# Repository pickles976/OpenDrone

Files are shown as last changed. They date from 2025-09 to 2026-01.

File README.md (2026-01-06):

# OpenDrone

OpenDrone is my attempt at creating a cheap, modular, easy-to-build and easy-to-fly series fixed-wing FPV drones. 

As a total beginner, I am learning as I go and prioritizing simplicity at every step. I try to avoid complex/skilled construction tricks.

I am making drones in different "weight" categories, starting with the [Mockingbird](./Mockingbird/README.md).

The goal is to have a collection of simple and cheap open-source drone designs with flight characteristics that make them useful tools, and not just toys. Long flight times, large payloads, modularity, and field-repairability are all design goals. The goal is to allow small groups of people to mass produce SAR drones without needing a whole lot of initial investment. A single maker or tinkerer should be able to assemble a small fleet of drones in their garage with a 3D printer, some hand tools, and [Made in China](https://evcraft.en.made-in-china.com) account.

## Educational Resources  

You can assemble one of these drones just by blindly following the build guide, but I also want to educate the end-user to enable them to modify and make their own drones. When I started this project, I had no knowledge of CAD, airplane design, or RC systems. I am still a novice, but I have the fundamentals down to build my own planes.

This list is by no means comprehensive, it is just the resources that *I* used. Feel free to open a pull request if you have suggestions. No higher education is needed to understand anything in this guide, just basic algebra and high school physics.

### Legal Stuff

Boring legal shit. Don't do anything illegal, please be respectful of others and their property. Don't get yourself in trouble.

#### AMA

The [Academy of Model Aeronautics](https://www.modelaircraft.org/) is a great resource. For about $90 a year you get $2.5M of liability insurance. Many clubs won't let you fly without a membership. They have a tool [here](https://www.modelaircraft.org/club-finder) for finding clubs and airfields near you.

#### FAA

The [FAA Rules](https://www.faa.gov/uas/recreational_flyers) has a lot of rules about flying drones. If you fly at a club, they will let you know all of the rules.

### Learning to Fly

Your local hobbyist club will hopefully be eager to teach you. I learned to fly on an HobbyZone Aeroscout in a few sessions. RealFlight is a simulator that costs about $90 and I have heard very good things about it, but have never tried it. For quad FPV, I recommend Liftoff simulator and a cheap [fpv sim controller](https://www.amazon.com/LiteRadio-Simulator-Controller-Platforms-Uncrashed-VelociDrone/dp/B0FMFCTSXV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) or something like the [Radiomaster Pocket](https://www.amazon.com/Radiomaster-Pocket-Transmitter-Lightweight-ELRS-Charcoal/dp/B0DXPLH726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) if you are willing to spend more money for a real controller.

### CAD Basics  

I use FreeCAD because this project should be accessible to as many people as possible. While other CAD programs are older, have more features, and are easier to use, but FOSS is under the control of the people. Not corporations or governments. For this reason, this guide is 100% FOSS.

[MangoJelly FreeCAD Tutorials](https://www.youtube.com/playlist?list=PLWuyJLVUNtc3UYXXfSglVpfWdX31F-e5S)  

The MangoJelly tutorials are incredible. He covers all of the fundamental skills needed to make parts in FreeCAD.  
(Total time to follow along with playlist, 24-48 hrs)  

[More FreeCAD Tutorials](https://youtube.com/playlist?list=PL10-2AjHWnW4To6a0luIpGCgNKQrAo04l&si=9Q5ZE8DqiylH0JF-)  

Here are more tutorials, with a guide on making a Lego minifigure based off of observation and measurements. These tutorials are excellent for thinking about how to replicate parts. Some of the first parts I designed were custom Lego accessories. (Total time to follow along with playlist, 10-20 hrs)

### Plastic Manufacturing Basics  

#### Plastic Part Design

It is easier to design good plastic parts if you understand the fundamentals of plastics and plastic design. The book [Designing Plastic Parts for Assembly](https://www.amazon.com/Designing-Plastic-Parts-Assembly-8E/dp/1569906688) is specifically about injection molding, but concepts like wall thickness, ribs, and filleting are applicable to 3D printed part design. I would recommend using the site [Anna's Archive](https://annas-archive.org/) to find a free copy of this book. It is very dense with a lot of information, so just read the first few chapters casually to understand the basics.

[Functional Design for 3D Printing](https://www.amazon.com/Functional-Design-Printing-2nd-Designing/dp/1511572027) is also a good resource.

#### 3D Printing

Personally I have a Bambu Labs A1 mini printer. It works extremely well out of the box with PLA and PETG filaments. For more pesky filaments like LW-PLA or TPU, you will need to play around with the settings to get things to work.

[Orca Slicer](https://orca-slicer.com/) is a fork of Bambu Studio with some added features. It is what I use for slicing my prints.

A video on [3D printing basics](https://www.youtube.com/watch?v=2vFdwz4U1VQ).  
[3D printing quality guide](https://www.youtube.com/watch?v=YPAXeBuq9qU)  

Here are some excellent videos on making snap-fit parts and making parts stronger:  
[Connecting Parts](https://www.youtube.com/watch?v=djm5tCFn9S0)  
[Part Strength](https://www.youtube.com/watch?v=Lq-SoGgKOcQ)  

### Aeronautical Engineering Basics

#### Forces of Flight

[A video on the Four Forces of Flight](https://www.youtube.com/watch?v=zKSNudPl9UI)  

#### Lift

[Principles of Flight (Lift)](https://www.youtube.com/watch?v=38X7UfPSdss)  
[Lift and Angle of Attack](https://www.youtube.com/watch?v=40uhfWbZH6g)  

#### Drag

Drag is a single force with multiple components. Parasitic Drag (consisting of skin friction drag and form drag), and Lift-Induced Drag (caused by turbulent airflow in the wake of the plane).

[Components of Drag](https://en.wikipedia.org/wiki/Drag_(physics))  
[Principles of Flight (Induced Drag)](https://www.youtube.com/watch?v=ohEiPg1q0TE)  
[Principles of Flight (Parasite Drag)](https://www.youtube.com/watch?v=V8vwyzt54_c)  

#### Tools

[Static Thrust Calculator](https://rcplanes.online/calc_thrust.htm)    
[ecalc](https://www.ecalc.ch/) prop sizing, performance estimation, much more.    

#### Airfoil Design

Airfoil design can get pretty complicated. I read a lot and ended up going with a simple Armin Wing, due to the fact that it would be nearly impossible for me to experimentally test a wing design without a wind tunnel or accurate cross-sectional measurements. However, wing design concepts are still good for understanding the basics of things like MAC and wing loading.
[Wing Design basics](https://www.youtube.com/watch?v=QHNtD8ChRZU)

I recommend watching these videos and building the glider from the video. Building the glider gave me a great sense of intuition for designing stable aircraft.
[RC Plane Design Basics](https://www.youtube.com/watch?v=CXvHv2EXcF8)
[Foamboard Glider Design](https://www.youtube.com/watch?v=YzqS_NjTxps)

#### Balance and Stability

[Aircraft Stability Concepts](https://www.youtube.com/watch?v=BWx8m4G0nEc)  
[Aircraft Stability Practical](https://www.youtube.com/watch?v=2t6tT77QFW4)  
[Flitetest, positioning the Center of Gravity](https://www.flitetest.com/articles/where-should-an-rc-airplane-center-of-gravity-be)  

### RC Basics

[Express LRS](https://www.youtube.com/watch?v=N0ajKoef3qs)  
[RC Battery Basics](https://www.youtube.com/watch?v=D98e2lRe2O8)   
[Safe Battery Charging](https://www.youtube.com/watch?v=MeAlEUb_vgg)
[Brushless DC Motors Explained](https://www.youtube.com/watch?v=yiD5nCfmbV0)  
[Servos](https://www.youtube.com/watch?v=tHOH-bYjR4k)  
[Joshua Bardwell Soldering](https://www.youtube.com/watch?v=GoPT69y98pY)  
[MuteFPV Soldering](https://www.youtube.com/watch?v=czXJevPWIsA)  
[SpeedyBee F405 wing setup](https://www.youtube.com/watch?v=LW57cibsMxY)  

[Flite Test Tutorial Series](https://youtube.com/playlist?list=PL6IuSFWz4ktvupu_gxw1vn-sjBGOkJFHV&si=_ucsjRaIemd7ZCSS) 

If you want to get deeper into electronics concepts, I recommend [Practical Electronics for Inventors, Fourth Edition](https://www.amazon.com/Practical-Electronics-Inventors-Fourth-Scherz/dp/1259587541)

### Autonomy

TODO

### FPV

TODO

# TODO: 

- [ ] stuff $100
    - [x] XT60 cable kit
    - [x] SG09 servos
    - [x] Fast-printing PETG
    - [x] FPV solder practice board
    - [x] Arms for holding boards while soldering
    - [x] brass sponge
    - [x] silicone mat
    - [x] flat plate for printing
    - [x] shorter servo connectors
- [ ] fpv
    - [ ] Eachine ev800D goggles
    - [ ] EWRF TS5823 5.8GHz 40CH 600mW FPV TX and camera

https://www.amazon.com/TMH-Adapter-Connector-Silicone-Battery/dp/B0DNT2R5JN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

# Further Reading
Aircraft Design a Conceptual Approach
Basics of Model Aircraft Design

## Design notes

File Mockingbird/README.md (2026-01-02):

# MockingBird

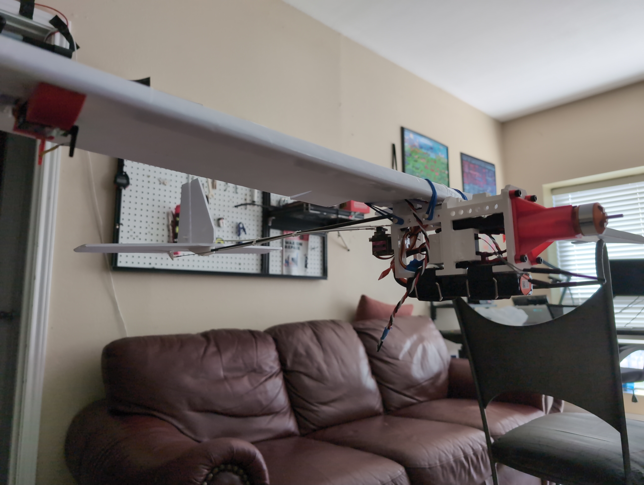
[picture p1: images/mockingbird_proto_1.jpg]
Mockingbird Prototype from Below

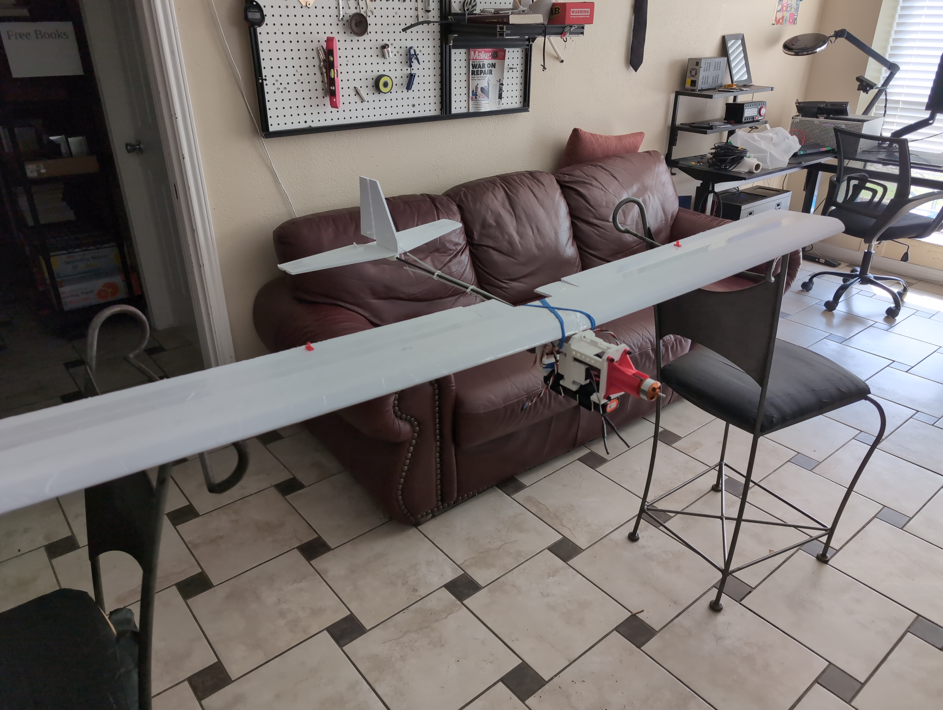
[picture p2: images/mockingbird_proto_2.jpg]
Mockingbird Prototype from above
  

Mockingbird is intended to be the cheapest and simplest drone to make. It has an initial setup cost of about $250 (not including tools), but the unit cost is about $90. Most of that is the electronics.

Every component is designed to fit on the printing plate of a Bambu A1 mini. The design is intended to be slow-flying and stable, with glider-like performance characteristics. The wings can be constructed out of a single piece of 20"x30" 5mm thick foamboard. The design supports multiple receivers and batteries, with variable wing positioning to adjust the center of gravity accordingly.

# Wing Specs

- Armin Wing Design
- 2 parts, 10" x 30" foamboard
- assembled dimensions
    - chord: 0.15m
    - wingspan: 1.524m
    - area: 0.2286m^2
- aspect ratio: 10.15 (wingspan squared over wing area)
- taper ratio: 1

An aspect ratio of 10 just barely puts us into glider territory. The wing design is a modified [Armin wing design](https://www.youtube.com/watch?v=karr67ZYho4) tweaked to take up exactly one sheet of 20"x30" foamboard.

### Equations
```math
Aspect Ratio = \frac SA
```

```math
\begin{aligned}
Wing Loading = \frac WA \\
Wing Loading = \frac 12 \rho V_{stall}^2 C_{Lift Max}  \\
V_{stall} = \sqrt{\frac {2\frac WA} {\rho C_{Lift Max}}} \\

\rho = 1.225 \\
C_{Lift Max} = 1.5

\end{aligned}
```

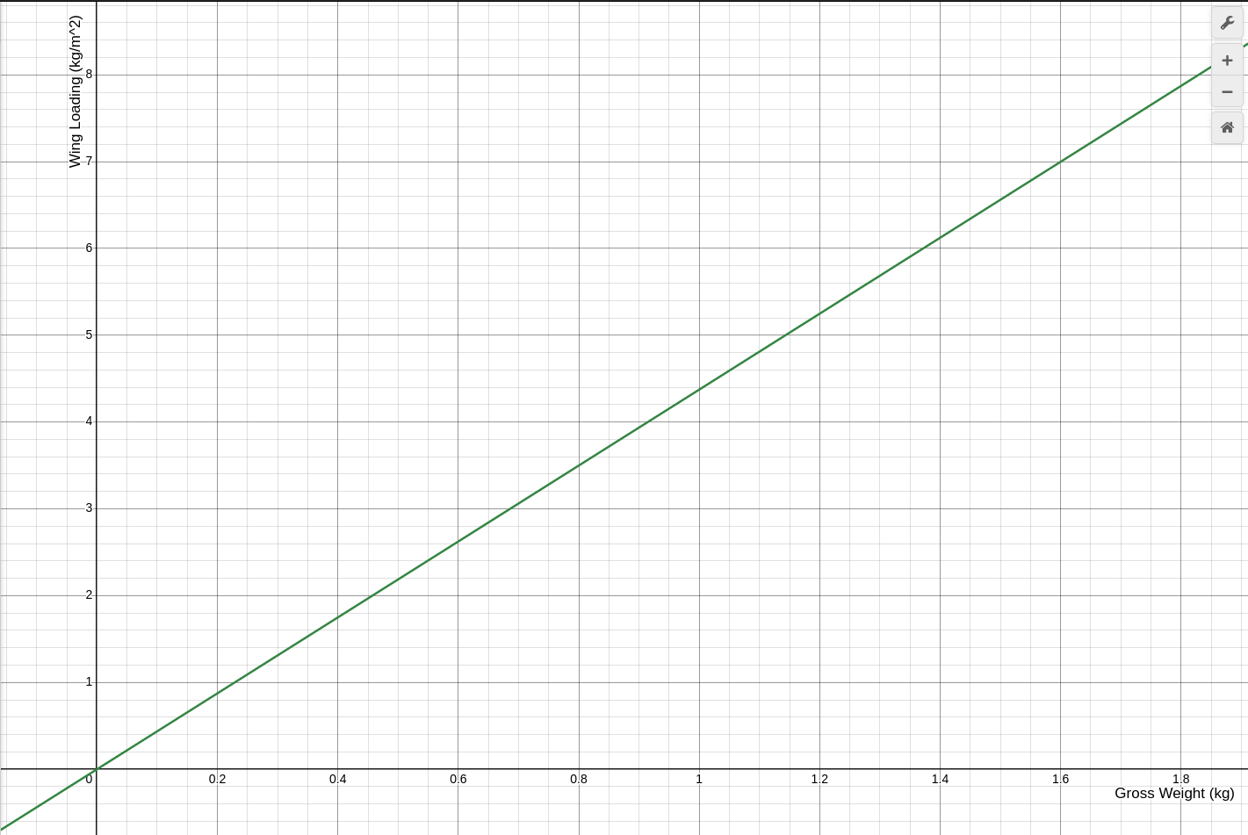
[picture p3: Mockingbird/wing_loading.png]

Wing Loading Curve  

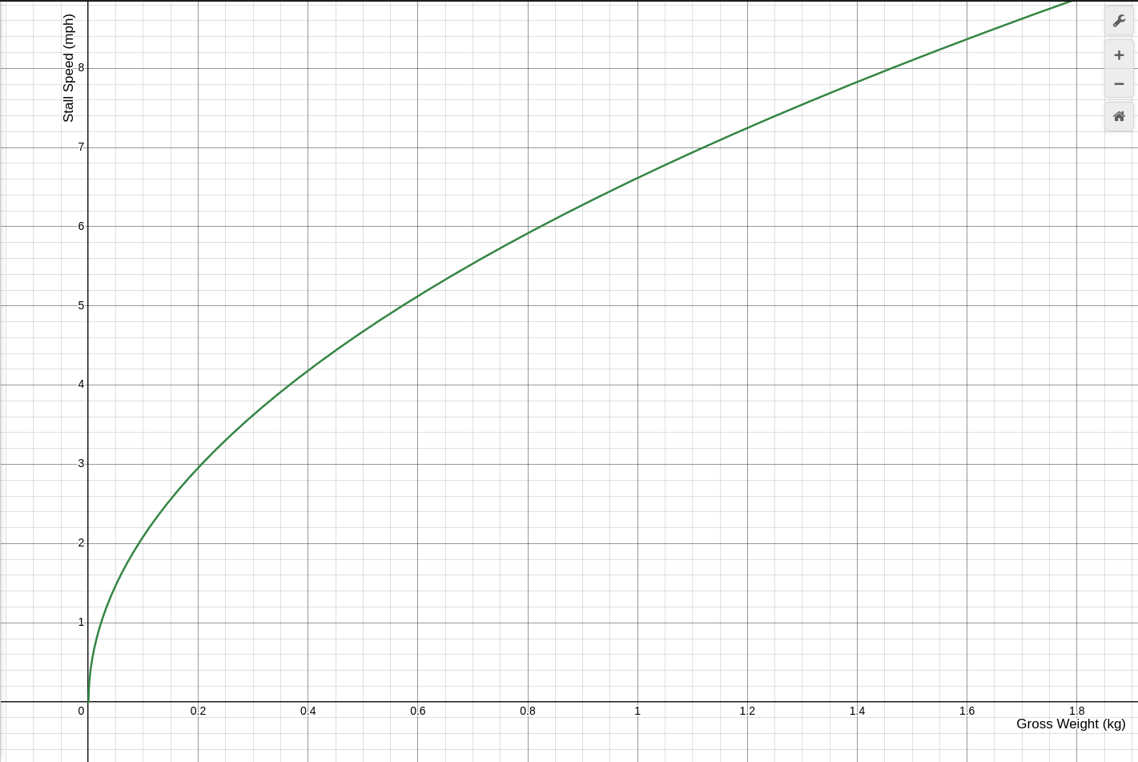
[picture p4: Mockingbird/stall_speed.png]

Stall Speed Curve   

Target weight is 650g, which would give us a stall speed of ~5mph.

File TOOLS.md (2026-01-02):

# Tools

An exhaustive list of tools required to build any of the designs in this guide.

## Assembly
Bambu A1 Mini or Larger $250
X-Acto knife $1 Harbor Freight
cutting surface $10
Printer
Metal Ruler $1
Large Hot Glue gun $20
Large Hot Glue sticks $10

## Control

RadioMaster Pocket $80
18650 Battery for radio (2x) $16
Battery Charger $30-$50

## Electronics

Pinecil soldering iron $40
100W USB-C charger for Pinecil $30

## Design

Digital Calipers (Vinca brand) $22

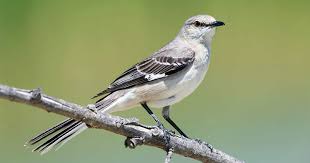
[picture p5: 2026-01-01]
images/mockingbird.jpeg

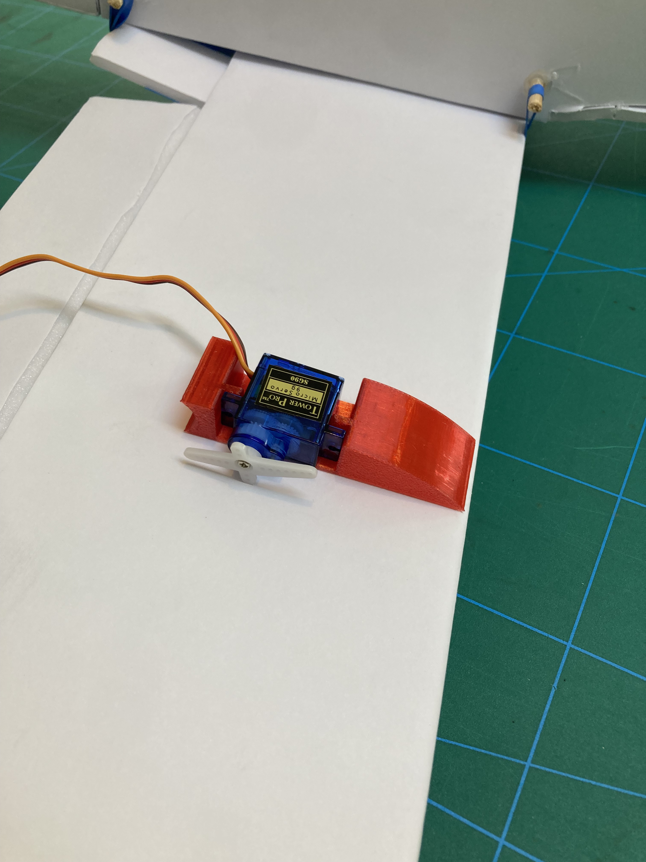
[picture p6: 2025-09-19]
images/servo_fairing.jpg

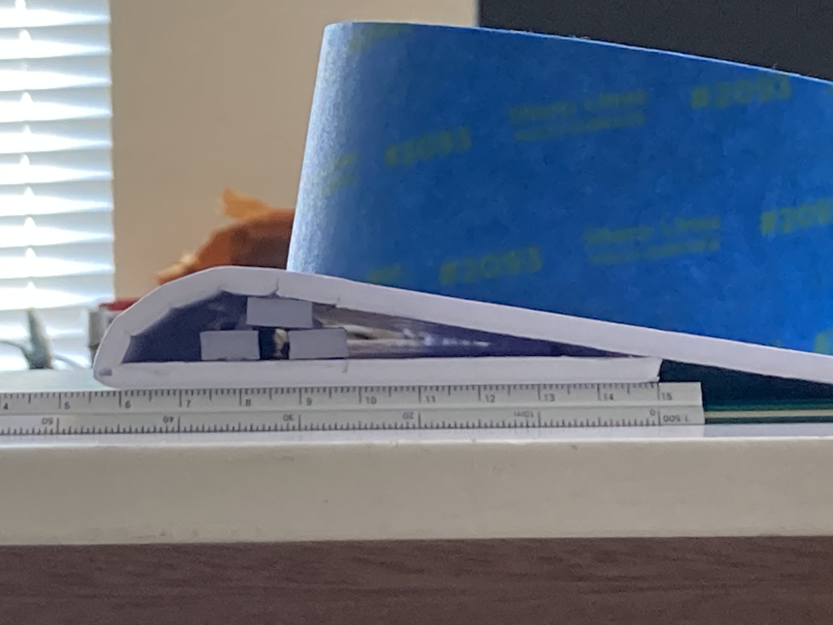
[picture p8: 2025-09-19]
Utilities/Reference Images/wing_cross_section.jpg

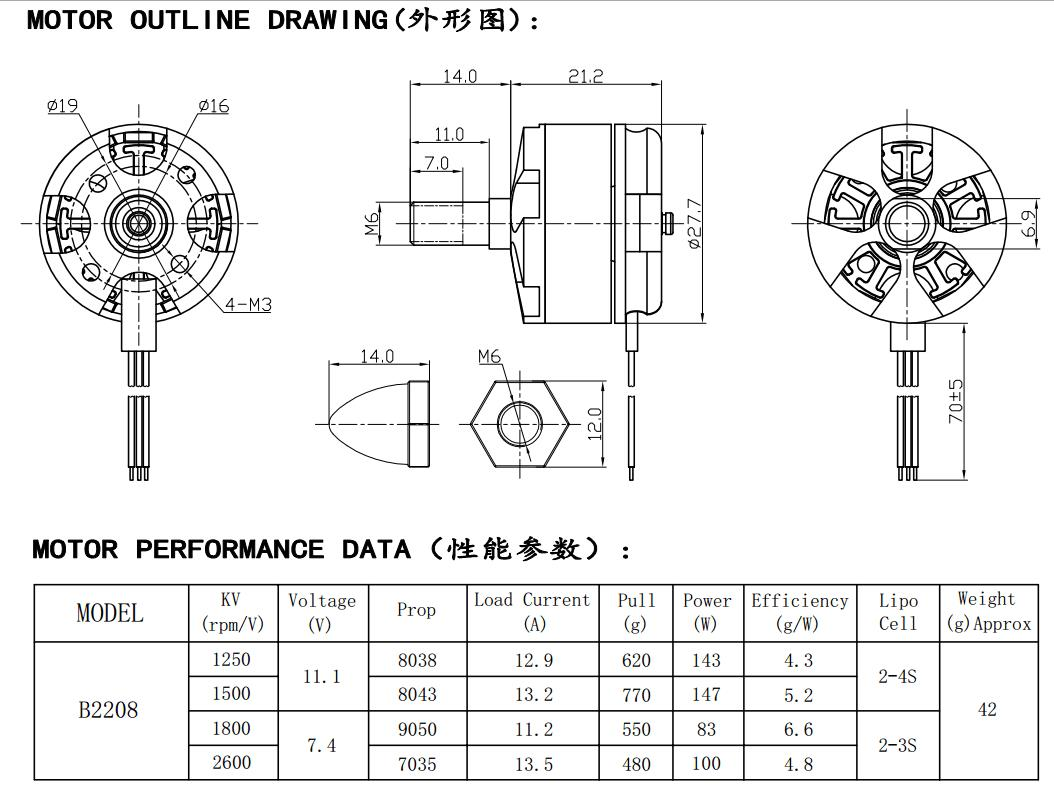
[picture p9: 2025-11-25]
Utilities/Reference Images/BR_2208.png

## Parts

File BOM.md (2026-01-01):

## Bill of Materials

20"x30" foamboard (2)
Carbon Fiber rod (5mm diameter) (2)
Wooden stake (5mm diameter) (2)
Servo fairings (2)
2S or 3S battery
Motor
Prop
Servo extenders
9g Servo (4)
front cap
end cap
tailfin
flight computer
ESC 

sticky side velcro
velcro straps
Lighweight PLA

## Cost

| Item | cost | qty for planes | cost per unit |
|---|---|---|---|
| Hook and Loop Velcro | 13 | 16 | 0.8125 |
| Adhesive Velcro | 10 | 360 | 0.02777777778 |
| M2 screws | 10 | 25 | 0.4 |
| Push rods | 13 | 10 | 1.3 |
| ELRS receiver | 19 | 1 | 19 |
| 30A ESC | 13 | 1 | 13 |
| 9g servo | 14 | 1 | 14 |
| 5x300mm carbon fiber rods | 10 | 5 | 2 |
| 3D printer filament | 50 | 20 | 2.5 |
| 0.8mm wire | 9 | 100 | 0.09 |
| 20"x30" 5mm foamboard | 54 | 18 | 3 |
| 5200mAh 2s | 22 | 2 | 11 |
| 800-1400kv motor | 12 | 1 | 12 |
| Dowels | 7 | 30 |  0.2333333333 |
| rubber bands |  5.3 | 32 | 0.165625 |
| servo extender | 10 | 2.5 | 4 |
| 8x4 properller | 12 | 3 | 4 |

Startup Cost: $283
Unit Cost $88

## Mass Budget

#### Electronics

| Item | Weight per unit | Qty | Total |
|---|---|-----|---|
| Battery | 172g | 1 | 172g  |
| ESC | 32g | 1 | 32g |
| Receiver | 15g | 1 | 15g |
| Motor | 41g | 1 | 41g |
| Servos | 12g | 4 | 48g |
| Servo Extender | 10g | 2 | 20g |
| Straps | ??? | ? | ??? |
| | | | 328g  |

#### Aerofoils

| Item | Weight per unit | Qty | Total |
|---|---|-----|---|
| Wings | 220g | 1 | 220g  |
| Carbon Fiber Rod | 11g | 2 | 22g |
| Wooden Stake | 2g | 2 | 4g |
| Servo Fairings | 3g | 2 | 6g |
| Tailfin Assembly | 27g | 1 | 27g |
| | | | 279g  |

#### Pod

| Item | Weight per unit | Qty | Total |
|---|---|-----|---|
| Motor Mount | 18g | 1 | 18g |
| Electronics Payload | 56g | 1 | 56g |
| M4 Screws | 3g | 8 | 24g |
| Servo Holder | ??? | 1 | ??? |
| Front Cap | ??? | 1 | ??? |
| End Cap | ??? | 1 | ??? |
| Body Fairing | ??? | 1 | ??? |
| | | | 88g |

TOTAL: 708g
ACTUAL MEASURED: 720g

#### Autonomy
flight computer -- 42g
GNSS -- 15g

# Tools 
x-acto knife
cutting surface
packing tape
fine sharpie
masking tape
squishy adhesive
twist ties
hex wrench set
small phillips head
hot glue gun
3D printer (Bambu A1 recommended)
PETG filament
LW-PLA filament
rubber bands
needle-nose pliers
scissors

## Optional
shrink-wrap
mallet

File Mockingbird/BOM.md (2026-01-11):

## Bill of Materials

2S 2200mAh battery   (1)  
SG09  Servo (4)  
30A Electronic Speed Controller (1)  
Motor (800-1400kv) (1)  
Servo extension cables (12") (2)  
Propeller (8x4E) (1)  
BetaFPV ELRS Mini Receiver (1)  

20"x30" foamboard (2)    
Carbon Fiber rod (5mm diameter) (2)    
Wooden Dowel (5mm diameter) (2)    
Adhesive velcro strips (2")  
Velcro straps (12") (2)  
PETG filament (100g)  
PLA or LW-PLA filament (100g)  
Hot Glue (100g)  

**Optional (for autonomy)**
SpeedyBee F405 Wing flight computer (1)  
Beitian BF-180GNSS module (1)

# Tools 
x-acto knife or snap-blade utility knife 
cutting surface (cutting mat on flat table)  
packing tape  
fine sharpie  
masking tape  
squishy adhesive  
twist ties  
hex wrench set  
small phillips head screwdriver (for servo screws)  
hot glue gun  
3D printer (Bambu A1 recommended)  
rubber bands  
needle-nose pliers  
scissors  

**Optional**  
shrink-wrap  
mallet  

## Cost

| Item | cost | qty for planes | cost per unit |
|---|---|---|---|
| Hook and Loop Velcro | 13 | 16 | 0.8125 |
| Adhesive Velcro | 10 | 360 | 0.02777777778 |
| M2 screws | 10 | 25 | 0.4 |
| Push rods | 13 | 10 | 1.3 |
| ELRS receiver | 19 | 1 | 19 |
| 30A ESC | 13 | 1 | 13 |
| 9g servo | 14 | 1 | 14 |
| 5x300mm carbon fiber rods | 10 | 5 | 2 |
| 3D printer filament | 50 | 20 | 2.5 |
| 0.8mm wire | 9 | 100 | 0.09 |
| 20"x30" 5mm foamboard | 54 | 18 | 3 |
| 5200mAh 2s | 22 | 2 | 11 |
| 800-1400kv motor | 12 | 1 | 12 |
| Dowels | 7 | 30 |  0.2333333333 |
| rubber bands |  5.3 | 32 | 0.165625 |
| servo extender | 10 | 2.5 | 4 |
| 8x4 properller | 12 | 3 | 4 |

Startup Cost: $283
Unit Cost $88

# Mass Budget

## Electronics

| Item | Weight per unit | Qty | Total |
|---|---|-----|---|
| Battery | 172g | 1 | 172g  |
| ESC | 32g | 1 | 32g |
| Receiver | 15g | 1 | 15g |
| Motor | 41g | 1 | 41g |
| SG 90 Servos | 19g | 4 | 36g |
| 12" Servo Extenders | 10g | 2 | 20g |
| Straps | ??? | ? | ??? |
| | | | 328g  |

## Aerofoils

| Item | Weight per unit | Qty | Total |
|---|---|-----|---|
| Wings | 220g | 1 | 220g  |
| Carbon Fiber Rod | 11g | 2 | 22g |
| Wooden Stake | 2g | 2 | 4g |
| Servo Fairings | 3g | 2 | 6g |
| Tailfin Assembly | 27g | 1 | 27g |
| | | | 279g  |

## Pod

| Item | Weight per unit | Qty | Total |
|---|---|-----|---|
| Motor Mount | 18g | 1 | 18g |
| Electronics Payload | 56g | 1 | 56g |
| M4 Screws | 3g | 8 | 24g |
| Servo Holder | ??? | 1 | ??? |
| Front Cap | ??? | 1 | ??? |
| End Cap | ??? | 1 | ??? |
| Body Fairing | ??? | 1 | ??? |
| | | | 88g |
  
TOTAL: 708g  
ACTUAL MEASURED: 720g  

## Autonomy
flight computer -- 42g
GNSS -- 15g

TOTAL + Autonomy: 780g

[Radiomaster Pocket ELRS](https://www.amazon.com/Radiomaster-Pocket-Transmitter-Lightweight-ELRS-Charcoal/dp/B0DXPLH726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)

[BetaFPV ELRS receiver](https://betafpv.com/products/elrs-micro-receiver?_pos=4&_sid=963b95d5a&_ss=r)

[Push Rods](https://www.amazon.com/Ltvystore-Stainless-Compatible-Airplane-Replacement/dp/B0B2LCJDPF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)

[Steel wire](https://www.amazon.com/Stainless-Straight-Wire0-8-1-6mmSpring-15-7nch/dp/B0C5VTGG1S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) 

Bambu PLA Aero
https://us.store.bambulab.com/products/pla-aero

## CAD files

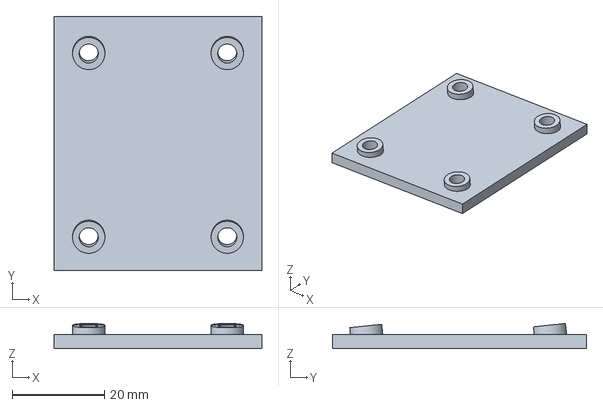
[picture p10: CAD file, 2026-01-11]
Mockingbird/CAD/Accessories/WingClamp.FCStd
45.0 x 55.0 x 5.43 mm

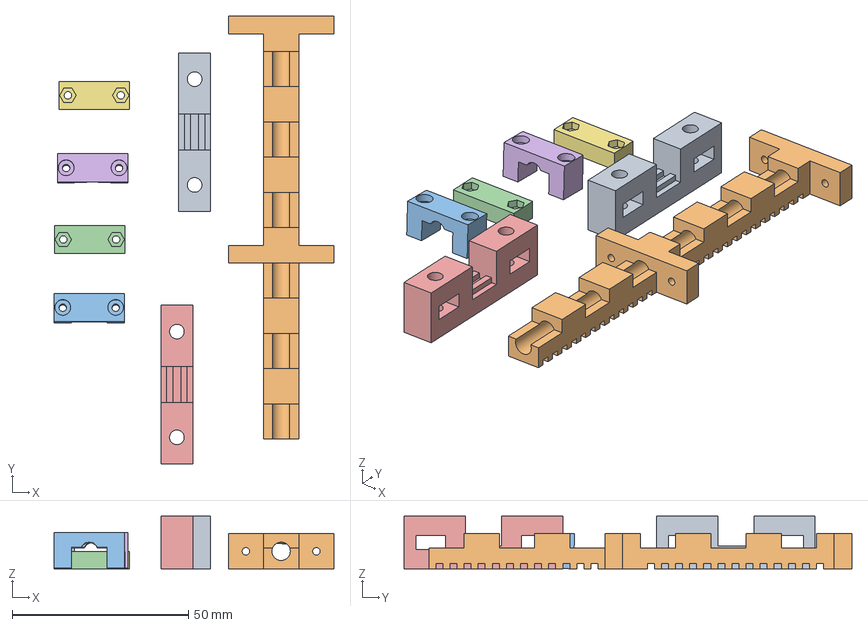
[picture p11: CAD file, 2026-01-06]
Mockingbird/CAD/GCODE/Mockingbird_WingSupports.3mf
79.4 x 127.0 x 15.0 mm
Mockingbird_V1_Proto-WingHolder.stl x 2
Mockingbird_V1_Proto-CFTube001.stl
Mockingbird_V1_Proto-CFClampTop.stl x 2
Mockingbird_V1_Proto-CFClampBottom.stl x 2

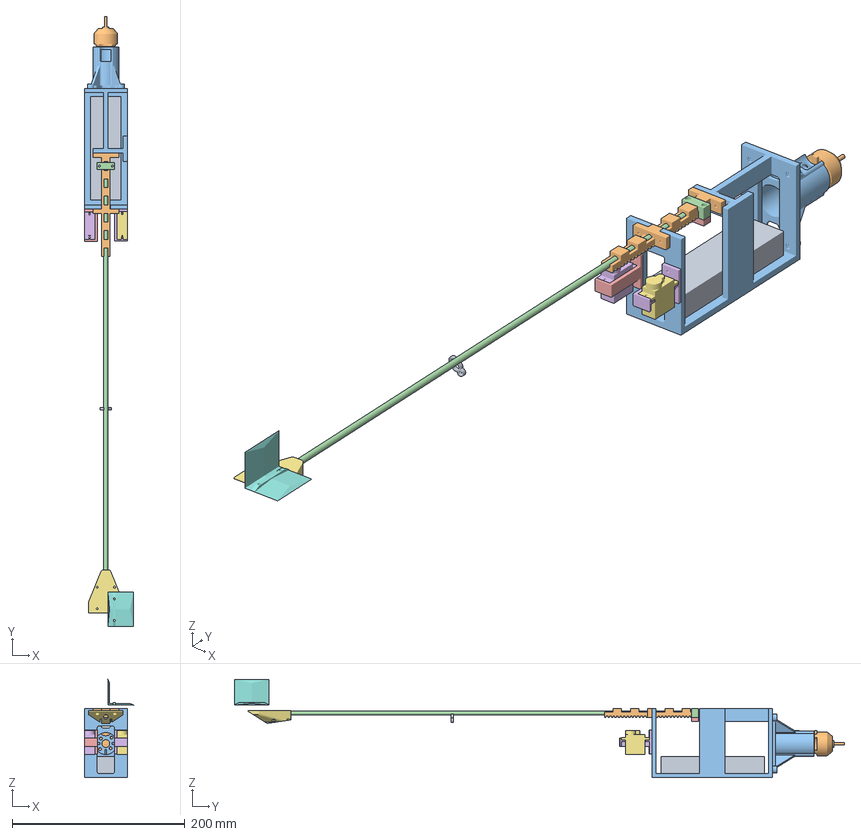
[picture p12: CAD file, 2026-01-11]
Mockingbird/CAD/Mockingbird_V1_Proto.FCStd
57.3 x 706.7 x 114.1 mm
BatteryRef
BR2208Ref
MotorMountV2
CFTubeRef
ServoMountPort
ServoMountStarboard
TailfinAdapter
TailfinReinforcement
WireGuide
CFTube001
EPayloadV5
CFClampTop
CFClampBottom
Servo9gRef002
Servo9gRef001

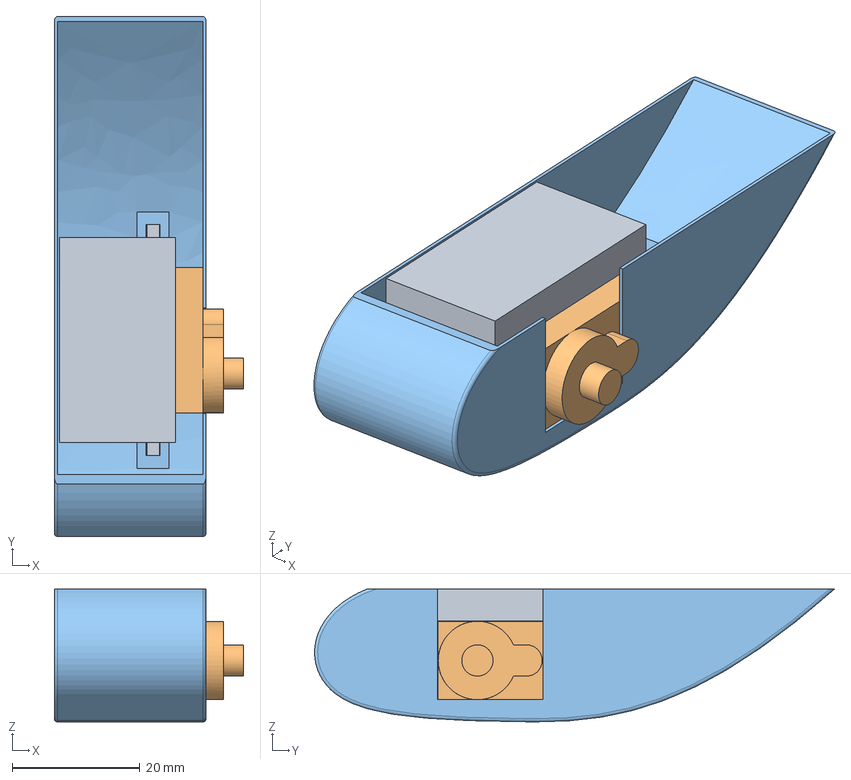
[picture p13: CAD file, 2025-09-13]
Mockingbird/CAD/ServoFairings/ServoFairing.FCStd
29.7 x 81.6 x 20.8 mm
Base
ServoRef
Fairing

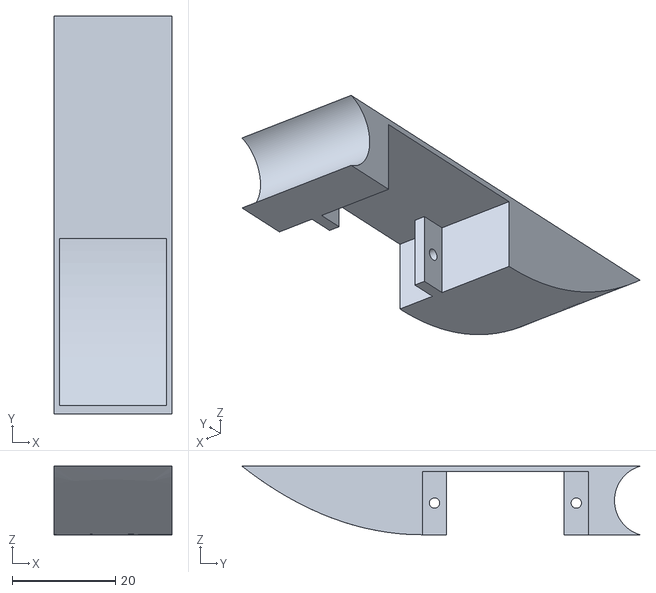
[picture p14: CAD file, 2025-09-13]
Mockingbird/CAD/ServoFairings/STL/ServoFairingV2-FairingTrailingEdge.stl
22.8 x 77.2 x 13.3

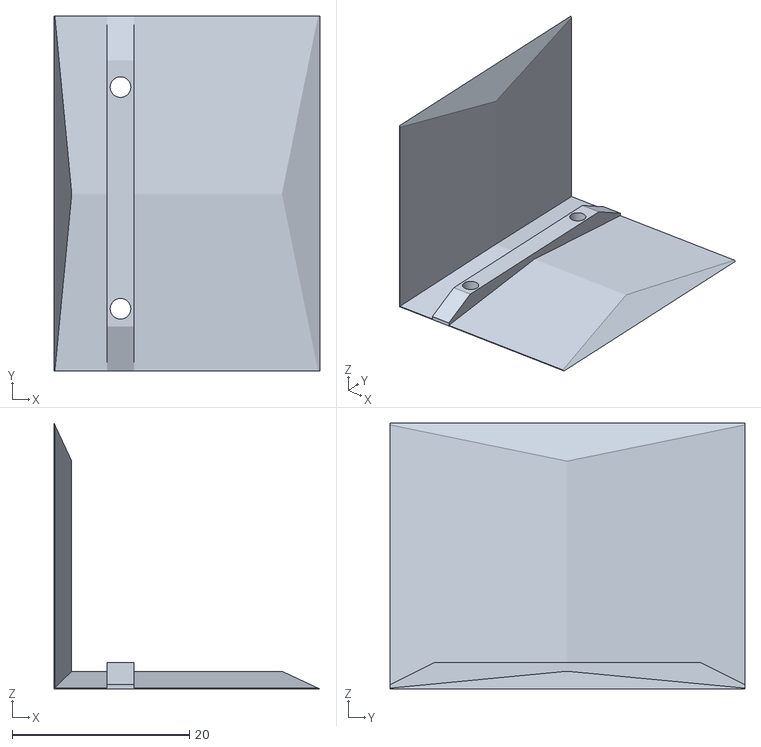
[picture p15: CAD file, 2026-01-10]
Mockingbird/CAD/STL/Mockingbird_V1_Proto-TailfinReinforcement.stl
30.0 x 40.0 x 30.0

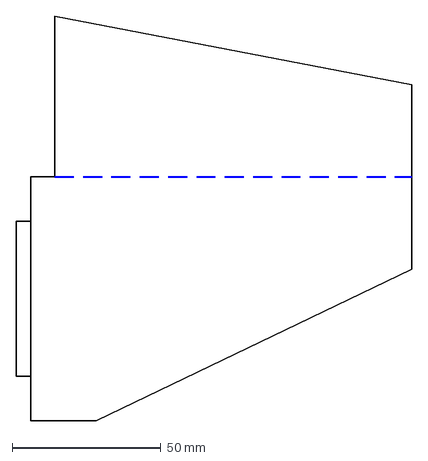
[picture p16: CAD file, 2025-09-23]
Mockingbird/CAD/Templates/DXF/tail_fin-VerticalStabilizer_layers.dxf
133.0 x 136.0 mm

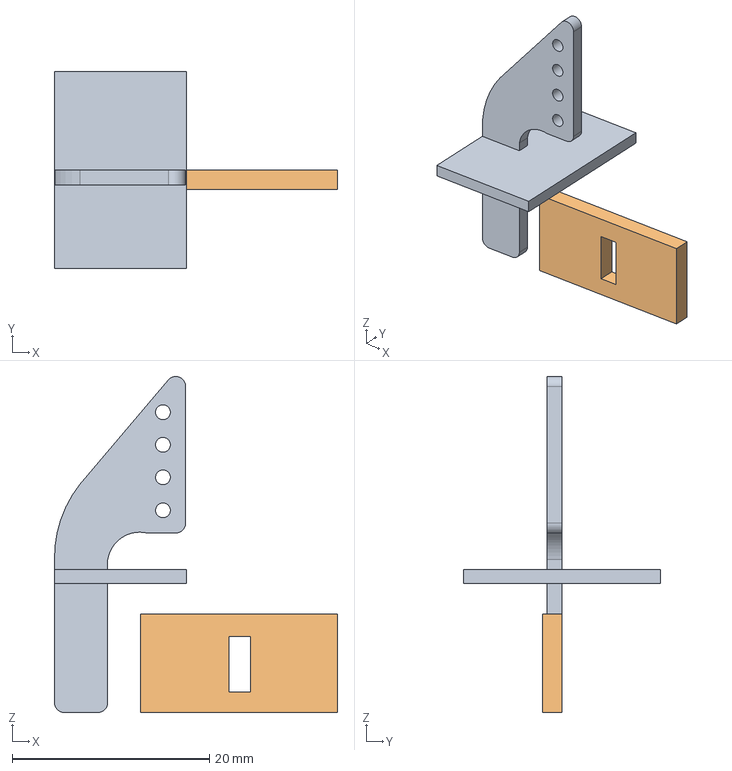
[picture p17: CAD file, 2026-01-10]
Mockingbird/CAD/Accessories/ControlHorns.FCStd
28.7 x 20.0 x 34.1 mm
Horns
Tab

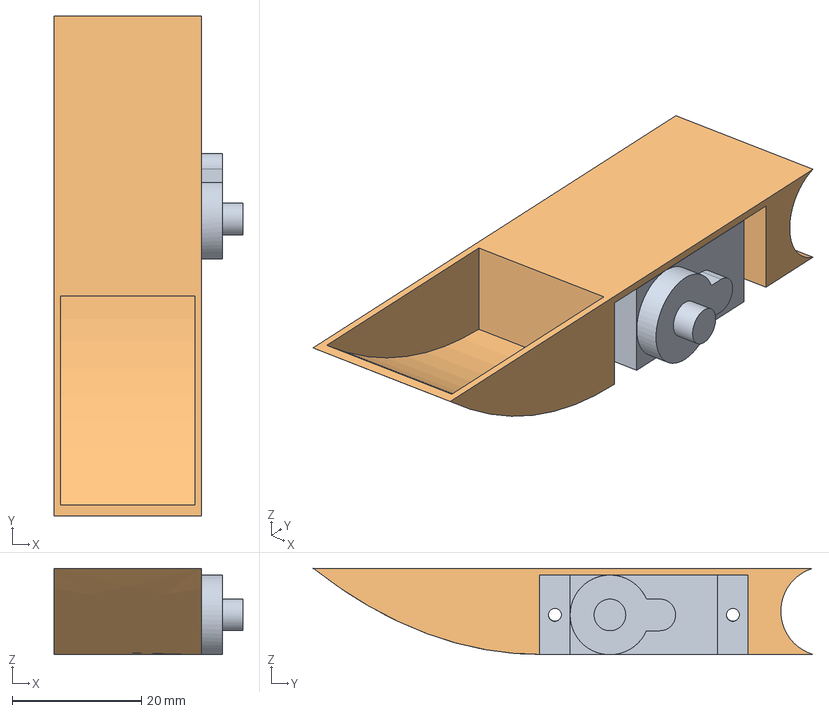
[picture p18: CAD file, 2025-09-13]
Mockingbird/CAD/ServoFairings/ServoFairingV2.FCStd
29.2 x 77.2 x 13.4 mm
ServoRef
Fairing

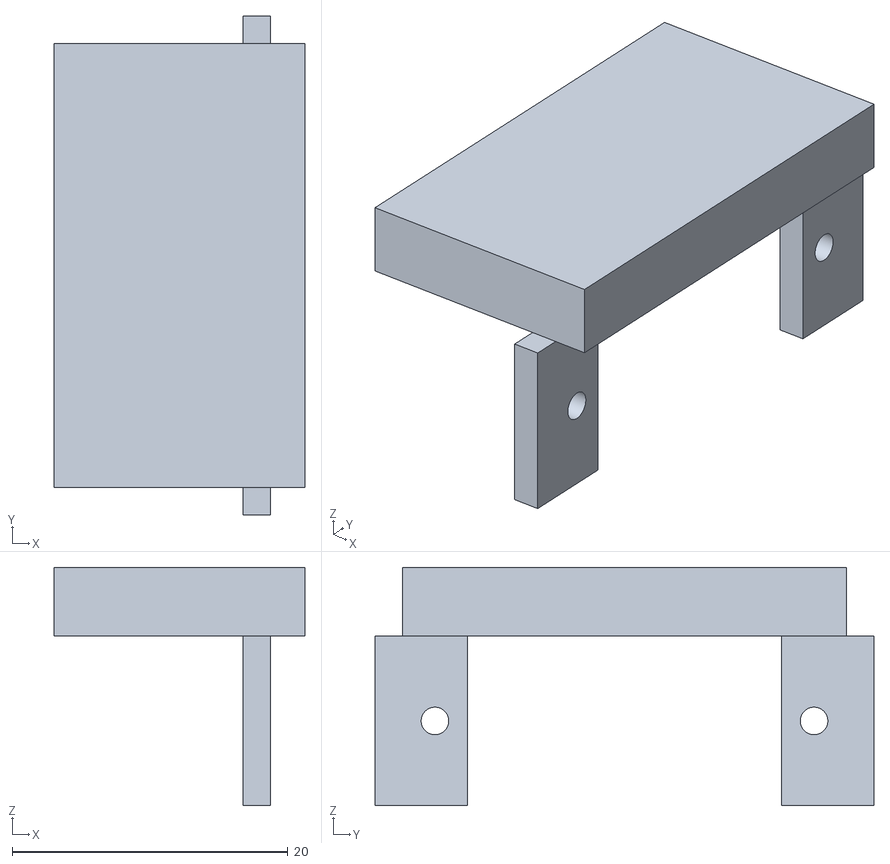
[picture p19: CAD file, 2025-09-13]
Mockingbird/CAD/ServoFairings/STL/ServoFairing-Base.stl
18.2 x 36.2 x 17.3

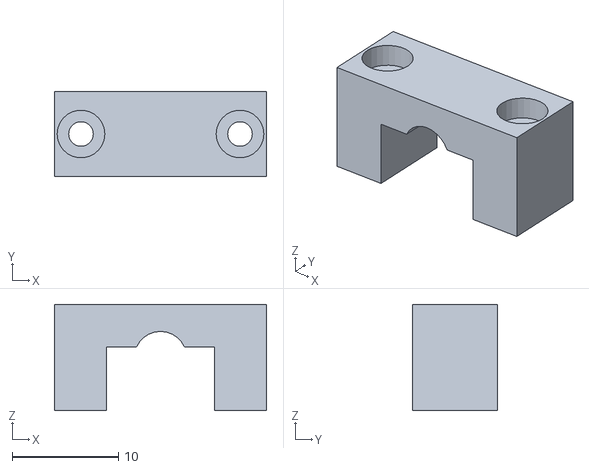
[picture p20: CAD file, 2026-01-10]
Mockingbird/CAD/STL/Mockingbird_V1_Proto-CFClampTop.stl
20.0 x 8.00 x 10.0

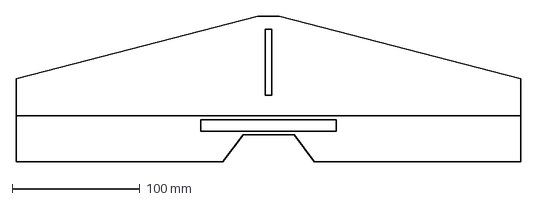
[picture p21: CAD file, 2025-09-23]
Mockingbird/CAD/Templates/DXF/tail_fin-HorizontalStabilizer.dxf
396.0 x 114.0 mm

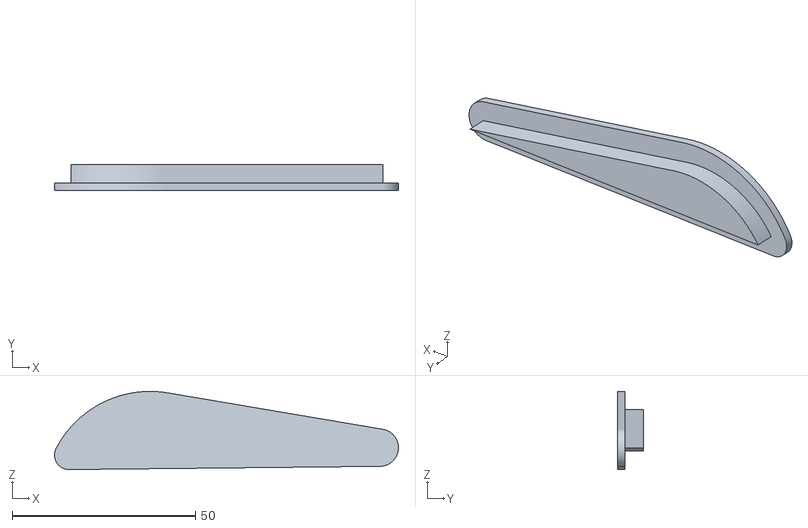
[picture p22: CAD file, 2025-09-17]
Mockingbird/CAD/Accessories/wing_endcap-Body.stl
93.7 x 7.00 x 21.3

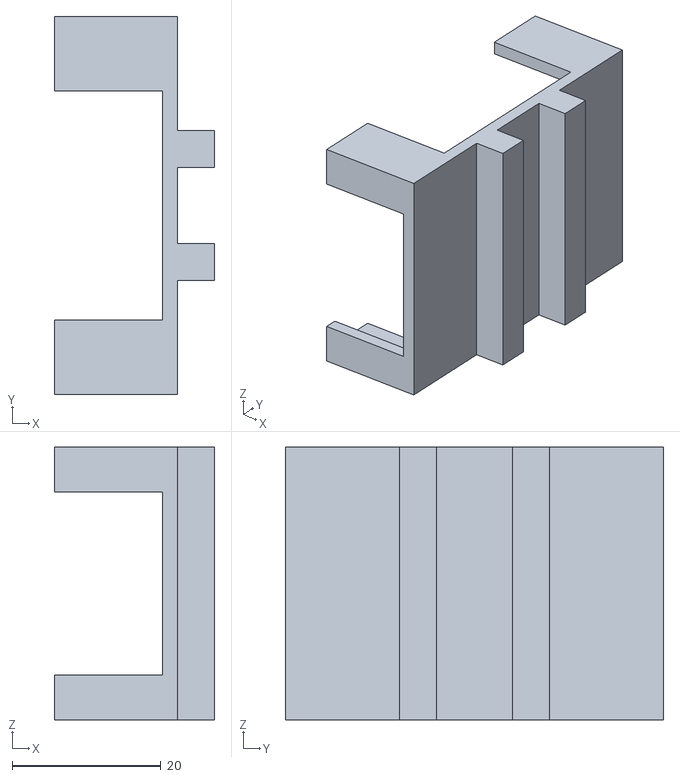
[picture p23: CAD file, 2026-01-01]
Mockingbird/CAD/PodEPayloadV1-SuperP ELRS Holder.stl
21.6 x 50.9 x 36.7

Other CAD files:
Mockingbird/CAD/Templates/pod.FCStd
Mockingbird/CAD/Templates/tail_rod_holder.FCStd
Mockingbird/CAD/ServoFairings/STL/ServoFairing-Fairing.stl
Mockingbird/CAD/STL/Mockingbird_V1_Proto-TailfinAdapter.3mf
Mockingbird/CAD/Accessories/Jigs.FCStd
Mockingbird/CAD/Accessories/Jigs_v2.FCStd
Mockingbird/CAD/Mockingbird_V1_Proto-ScrewTestPart.stl
Mockingbird/CAD/STL/BR2208 Racerstar - 1400 kv.STEP
Mockingbird/CAD/STL/ControlHorns-Horns.stl
Mockingbird/CAD/STL/ControlHorns-Tab.stl
Mockingbird/CAD/STL/Mockingbird_V1_Proto-CFClampBottom.stl
Mockingbird/CAD/STL/Mockingbird_V1_Proto-CFTube001.stl
Mockingbird/CAD/STL/Mockingbird_V1_Proto-EPayloadV5.stl
Mockingbird/CAD/STL/Mockingbird_V1_Proto-ElectronicsPayload.stl
Mockingbird/CAD/STL/Mockingbird_V1_Proto-MotorMountV2.stl
Mockingbird/CAD/STL/Mockingbird_V1_Proto-ScrewTestPart.stl
Mockingbird/CAD/STL/Mockingbird_V1_Proto-ServoMountPort.stl
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

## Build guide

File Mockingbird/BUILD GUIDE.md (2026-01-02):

# BUILDING GUIDE

## Electronics Setup

## 3D Printed Parts

## Wings and Tailfin

## Control Surfaces and Pushrods

## Final Assembly

## Tips and Tricks

**Print the Electronics Payload at an angle on the Bambu A1 Mini**
There may be temperature issues at the edges of the printing plate on the Bambu A1 mini. Try printing it at an angle to see if that helps at all.

**Do your wing balancing before you cut your push rods for the tailfin control surfaces to length**   
It is easier to adjust your balance by moving the tailfin length, so the length of your tailfin will be dependent on the balance. Once that is determined, then you can adjust the length of your pushrods.

**Use 1.2mm wire control rods for tail control surfaces**  
The tail control surfaces are far away from the servos, and 0.64mm piano wire will deform. 1.2mm wire is thick enough to withstand the forces, while also deflecting the desired amount along its path from the servo to the control surface.

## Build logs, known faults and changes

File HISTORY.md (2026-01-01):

# History

Here is some history of the project to prove I didn't know anything about drones before starting.

Playing around with foam to figure out how big the pod needs to be:  
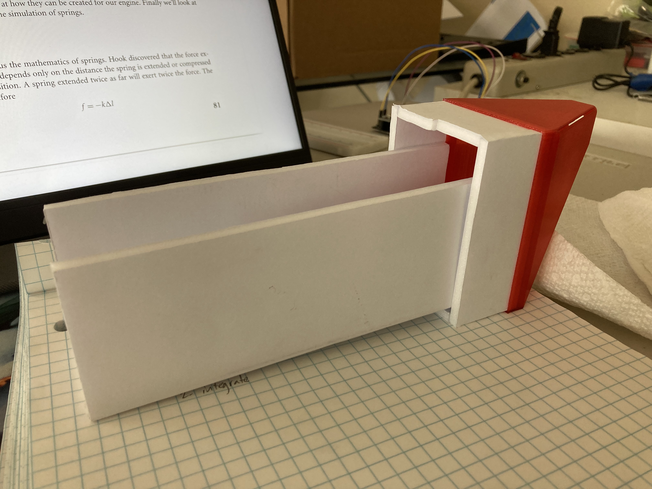
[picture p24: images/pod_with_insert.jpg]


First Wings:  
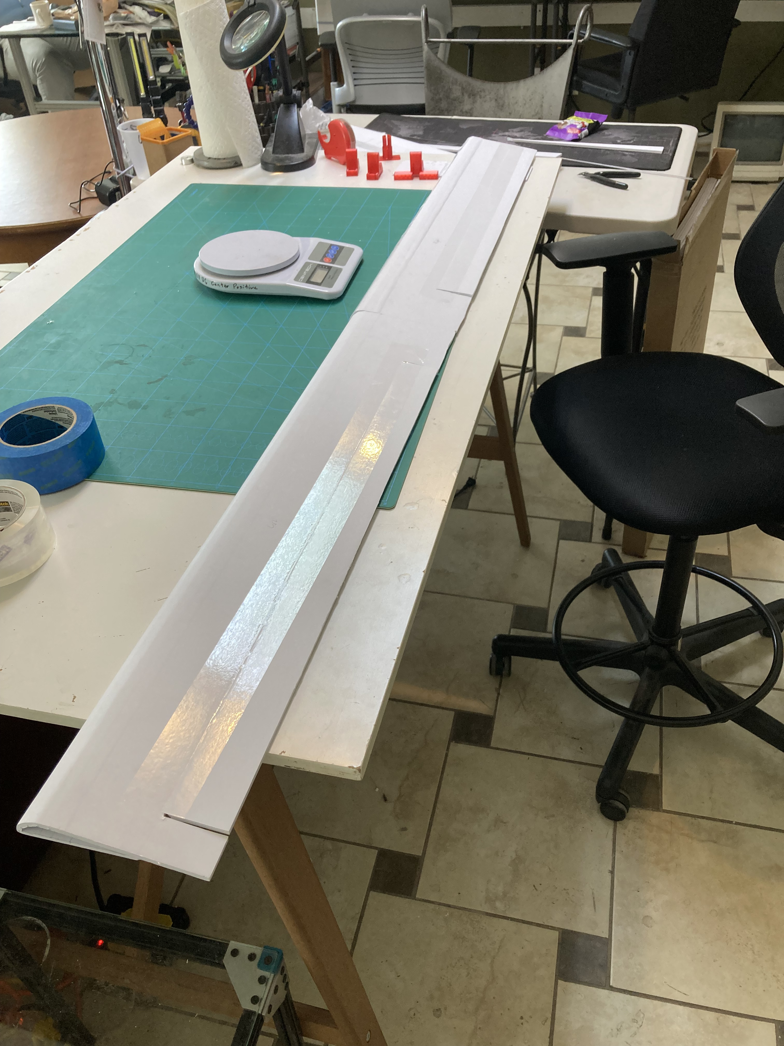
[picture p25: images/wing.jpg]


Pod and Wings:  
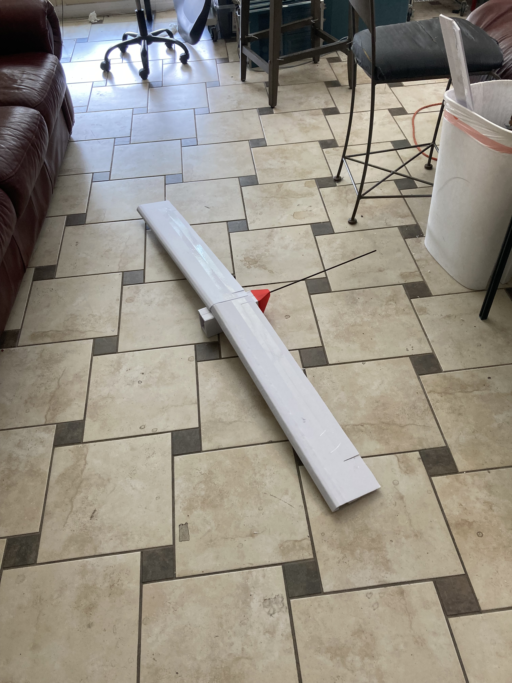
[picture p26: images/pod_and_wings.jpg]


Mockingbird "Payload" first print:  
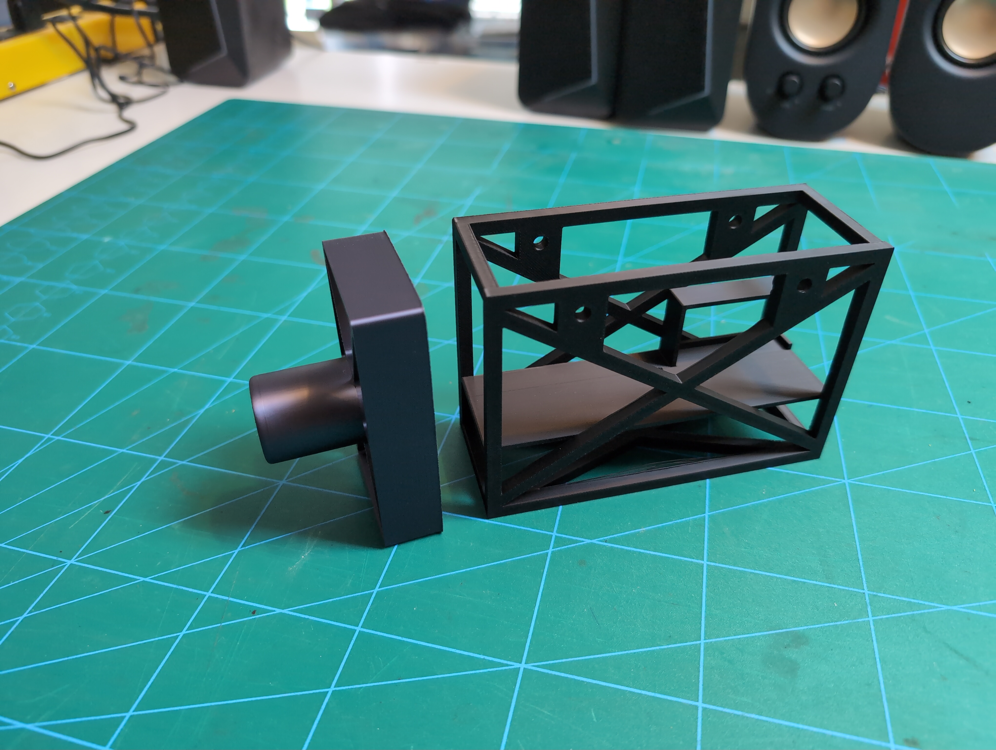
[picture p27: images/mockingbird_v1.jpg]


Mockingbird "Payload" second print:  
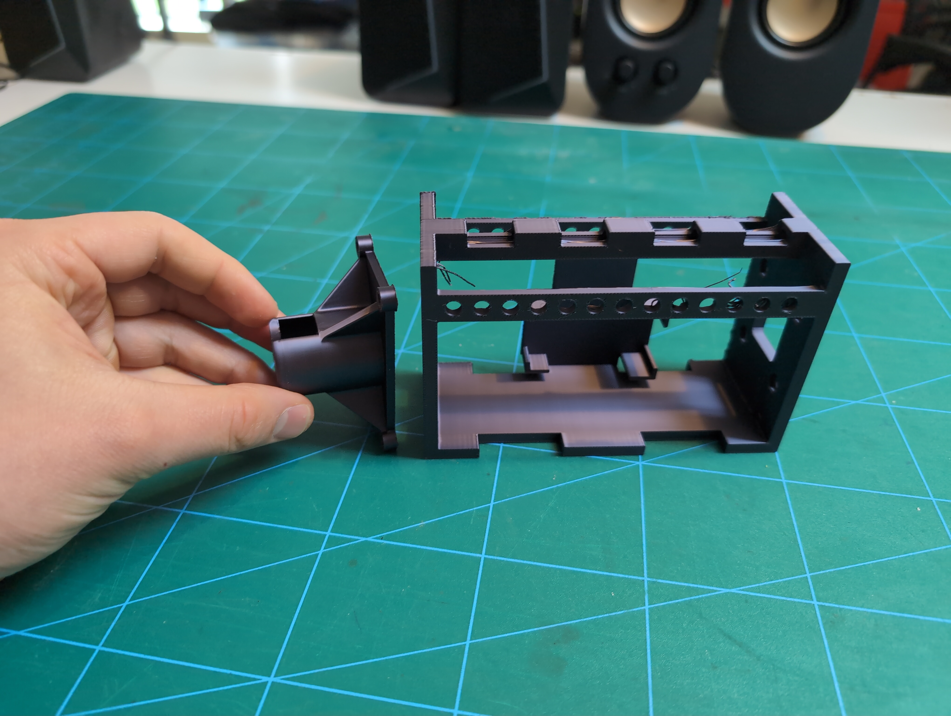
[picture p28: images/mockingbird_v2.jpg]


Mockingbird prototype wing balancing test:  


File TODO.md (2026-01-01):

# TODO

### CAD

#### Design Improvement

- [ ] print new cantilevered pod
- [ ] what improvements can be made to cantilevered pod?

- [ ] design some kind of locking mechanism for the pod case

- [ ] add cable runs for rear elevator for tailfin adapter piece
- [ ] re-design control horns (surface mount instead of thru-hole)
- [ ] redesign control surfaces on tailfin
- [ ] add hole to pod template for top and for receiver antenna
- [ ] design clamping tailfin holder with M2 screws/nuts and PETG
- [ ] change nut sizes in pod to M2
- [ ] remove material from center of wings, make hole for servo cables smaller

#### Re-print with new designs
- [ ] figure out LW-PLA
- [ ] re-print pod in LW-PLA
- [ ] re-print tailfin adapter with LW PLA

#### Redo Plane
- [ ] remake tailfin assembly
- [ ] redo control rod setup

# PROTOTYPE COMPLETE AND READY TO FLY

### Design Fairings
- [ ] front cover
- [ ] rear cover

### Make a New one and give it away

Questions:
- how long did it take to make?
- how many materials did it require?

### Template Updates
- [ ] update wing CAD file
    - [ ] attach fairing 14" down wing, 5mm away from leading edge
    - [ ] 7" piano wire length, 70mm actuation distance
    - [ ] 10x20mm hole in the wing next to the fairing
- [ ] is servo direction going to end up mattering? (probably, yes)
- [ ] design left and right wing fairings differently

- [ ] update all templates with control surface locations and other things
- [ ] combine all templates into printable pdfs
    - [ ] wings
    - [ ] horizontal stabilizer
    - [ ] vertical stabilizer
    - [ ] wing spars
    - [ ] pod
    - [ ] pod spars
    - [ ] payload insert

### 3D CAD Updates
- [ ] clean up all the CAD files

- [ ] update design documents
- [ ] add obsidian notes to design docs

### Engineering Docs
- [ ] interface control document
- [ ] power budget
- [ ] mass growth allowance
- [ ] TRL assessment
- [ ] iterate

Inspirations:
https://www.thingiverse.com/thing:7187147

[Radiomaster Pocket ELRS](https://www.amazon.com/Radiomaster-Pocket-Transmitter-Lightweight-ELRS-Charcoal/dp/B0DXPLH726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)

[BetaFPV ELRS receiver](https://betafpv.com/products/elrs-micro-receiver?_pos=4&_sid=963b95d5a&_ss=r)

[Push Rods](https://www.amazon.com/Ltvystore-Stainless-Compatible-Airplane-Replacement/dp/B0B2LCJDPF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)

[Steel wire](https://www.amazon.com/Stainless-Straight-Wire0-8-1-6mmSpring-15-7nch/dp/B0C5VTGG1S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) 

Bambu PLA Aero
https://us.store.bambulab.com/products/pla-aero

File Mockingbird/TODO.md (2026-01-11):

# TODO

- [ ] Finish 3D CAD design and printing profiles
- [ ] Clean up and finalize templates
- [ ] Full step-by-step assembly guide
- [ ] Film full step-by-step guide

## 3D CAD

Wing screw-in hole spacing: 40mm long, 30mm wide

### Design Improvement

**SUNDAY**
- [x] print wing top support thing
- [x] move servo down 5mm
- [ ] redesign wing clamp and get it working
    - [ ] figure out what angle is required
    - [ ] print
    - [ ] attach

- [ ] figure out how to print LW-PLA successfully

#### Case
- [ ] design some kind of locking mechanism for the pod case
- [ ] top case
- [ ] bottom case

- [ ] front case
- [ ] rear case

# PROTOTYPE FINISHED!

# Pre-Release Cleanup

### Template Updates
- [ ] update wing CAD file
    - [ ] remove material from center of wings, make hole for servo cables smaller
    - [ ] attach fairing 14" down wing, 5mm away from leading edge
    - [ ] 7" piano wire length, 70mm actuation distance
    - [ ] 10x20mm hole in the wing next to the fairing
    - [ ] add annotations to wing drawing

- [ ] update all templates with control surface locations and other things
- [ ] combine all templates into printable pdfs
    - [ ] wings
    - [ ] horizontal stabilizer
    - [ ] vertical stabilizer
    - [ ] wing spars

### Make a New one and give it away
- [ ] design cutting jigs

Questions:
- how long did it take to make?
- how many materials did it require?

### Create .3mf files
- [ ] PLA
- [ ] PETG
- [ ] LW-PLA

### Fly It
- [ ] get images of it flying
- [ ] export to 3D model for viewing in browser
- [ ] create a website

### Create Step-By-Step construction guide
- [ ] markdown with images
- [ ] video

### Engineering Docs
- [ ] interface control document
- [ ] power budget
- [ ] mass growth allowance
- [ ] TRL assessment
- [ ] iterate

Inspirations:
https://www.thingiverse.com/thing:7187147

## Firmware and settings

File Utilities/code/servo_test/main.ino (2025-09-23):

#include <ESP32Servo.h>
    
Servo myServo; // Create a servo object
const int servoPin = 18; // Define the GPIO pin for the servo

void setup() {
  myServo.attach(servoPin); // Attach the servo object to the pin
}

void loop() {
  myServo.write(0); // Move to 0 degrees
  delay(1000);
  myServo.write(90); // Move to 90 degrees
  delay(1000);
  myServo.write(180); // Move to 180 degrees
  delay(1000);
}

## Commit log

2025-09-13 Init commit
    [ControlHorns.FCStd, Jigs.FCStd, Jigs_v2.FCStd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]
2025-09-17 Added some more parts
    [#electronics_insert_layered.dxf, electronics_insert-Body.dxf, electronics_insert.FCStd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]
2025-09-17 Pod design completed
    [#pod.dxf, pod.FCStd]
2025-09-19 Added some stuff to the TODO: list
    [tail_fin.FCStd]
2025-09-23 Lots of changes
    [#pod.dxf, #tail_fin-HorizontalStabilizer.dxf, electronics_insert.FCStd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]
2025-11-25 Updated CAD
    [BR2208 Racerstar - 1400 kv.STEP, FlySky FS-iA6B Receiver Holder.stl, PodEPayloadV1-Body.stl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]
2025-12-27 Added motor mount
    [MotorMount.stl, PodEPayloadV1-EPayloadPad007.stl, PodEPayloadV1.FCStd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]
2025-12-28 Total rework of the electronics payload
    [MotorMount.stl, PodEPayloadV1-EPayloadV2.stl, PodEPayloadV1-MotorMountV2.stl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]
2025-12-30 Redesign (again)
    [MotorMount.stl, PodEPayloadV1-EPayloadV2.3mf, PodEPayloadV1-EPayloadV2.stl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]
2025-12-30 Updated TODO
    [PodEPayloadV1-Body.stl, PodEPayloadV1-EPayloadPad007.stl, PodEPayloadV1-FS-IA6B Holder.stl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]
2025-12-31 Got a lot of stuff done
    [#electronics_insert_layered.dxf, #pod.dxf, #tail_fin-HorizontalStabilizer.dxf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]
2025-12-31 Updated electronics payload
    [PodEPayloadV1-MotorMountV2.stl]
2025-12-31 Removed shit
    [PodEPayloadV1.FCStd]
2026-01-01 Lots of updates
    [PodEPayloadV1-ElectronicsPayload.stl, PodEPayloadV1-SuperP ELRS Holder.stl, PodEPayloadV1.FCStd]
2026-01-01 Big refactor and cleanup
    [#pod.dxf, BR2208 Racerstar - 1400 kv.STEP, ControlHorns-Horns-Nylon.stl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]
2026-01-02 Remade payload
    [Mockingbird_V1_Proto.FCStd]
2026-01-02 Updated again
    [Mockingbird_V1_Proto.FCStd]
2026-01-04 Updated e-payload design
    [Mockingbird_V1_Proto.FCStd]
2026-01-06 Redesigned POD again
    [Mockingbird_V1_Proto.FCStd, Mockingbird_V2_Proto-ElectronicsPayload.stl]
2026-01-06 Total rehaul of e-payload again
    [Mockingbird_V1_Proto-EPayloadV5.stl, Mockingbird_V1_Proto-ScrewTestPart.stl, Mockingbird_V1_Proto.FCStd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]
2026-01-06 Updated CAD and docs
    [Mockingbird_V1_Proto-CFClampBottom.stl, Mockingbird_V1_Proto-CFClampTop.stl, Mockingbird_V1_Proto-CFTube001.stl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]
2026-01-10 Updated a lot of stuff
    [ControlHorns-Horns.stl, ControlHorns-Tab.stl, ControlHorns.FCStd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]
2026-01-11 Updated stuff
    [Mockingbird_V1_Proto.FCStd, WingClamp.FCStd]
